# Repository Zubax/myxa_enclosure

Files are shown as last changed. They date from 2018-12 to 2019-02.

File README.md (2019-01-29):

# Aluminum enclosure for Myxa

[**Myxa**](https://zubax.com/products/myxa) is a high-end FOC ESC based on the [Télega motor control technology](https://zubax.com/technologies/telega).

The aluminum enclosure increases the continuous power range up to 850W and provides additional protection against mechanical damage.

You need to have SolidWorks 2017sp1 or higher to open the assembly files. You can also download [eDrawings](http://www.edrawingsviewer.com) for viewing and exporting the enclosure assembly files.

A plastic enclosure for Myxa is [also available](https://www.thingiverse.com/thing:2792733).

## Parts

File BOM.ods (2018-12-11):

Qty | Device | Parts | Description | SIZE | DIGIKEY# | LENGTH | MANF | MANF# | link
3 | HEATSHRINK |  | Heatshrink for phase connectors | D = 4.6mm | X2-4.0-0-SP | 10mm | TE Connectivity Raychem Cable Protection | X2-4.0-0-SP
1 | HEATPAD |  | Heatpad | 35x8x1 mm | P121365-ND |  | Panasonic Electronic Components | EYG-T3535A10A | https://www.chipdip.ru/product0/9000203898
3 | Screw M2.5 15mm DIN912 ISO4762 |  | Mounting screws | M2.5 15mm | 36-29306-ND | ~15mm | Keystone Electronics | 29306 | https://www.mcmaster.com/91290a302
1 | Housing |  | Aluminum housing for Myxa |  |  |  | Zubax | Myxa housing
1 | Printed mount |  | 3d-printed part which serves as standoffs and big capacitor damper |  |  |  | Zubax | Myxa printed part

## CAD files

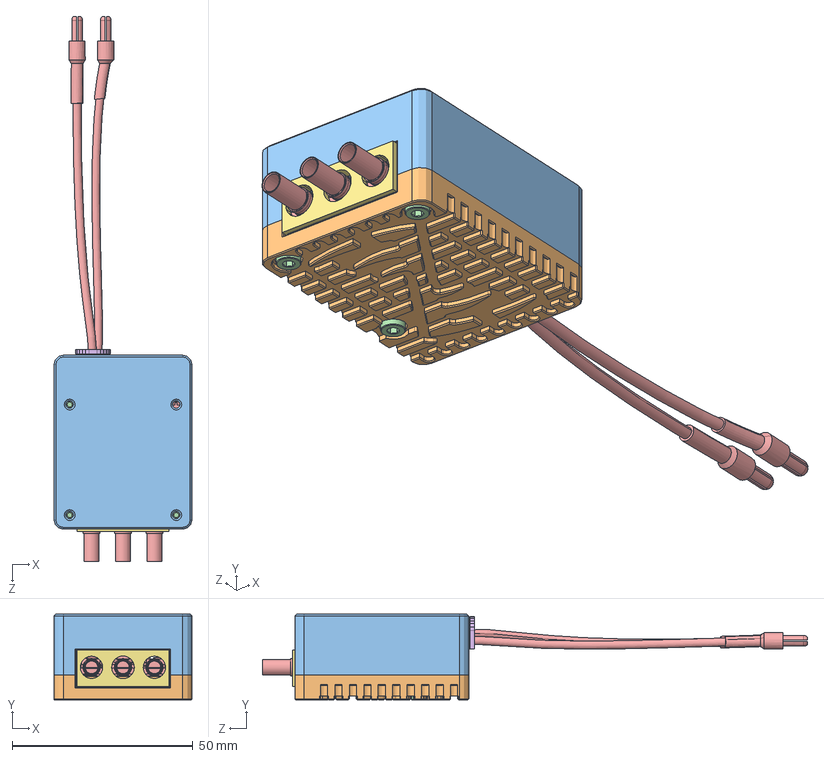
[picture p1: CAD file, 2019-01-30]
myxa_case.sldasm
38.2 x 23.7 x 151.0 mm
washer x 6
case_top
case_bottom
91290A302_BLACK-OXIDE ALLOY STEEL SOCKET HEAD SCREW x 3
myxa
battery_wires_spacer
phase_insert

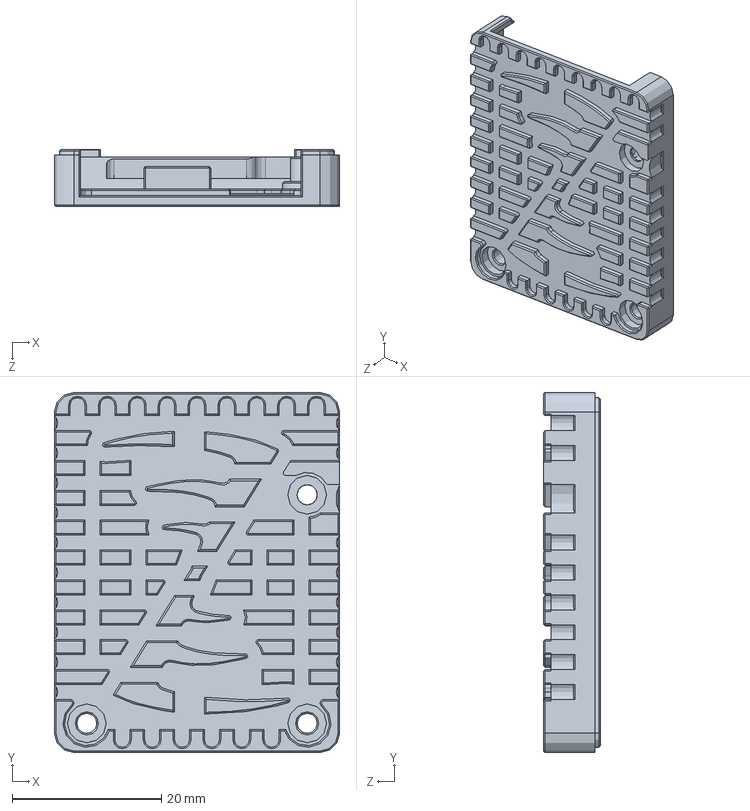
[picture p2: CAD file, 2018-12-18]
case_top.sldprt
38.2 x 48.2 x 7.65 mm

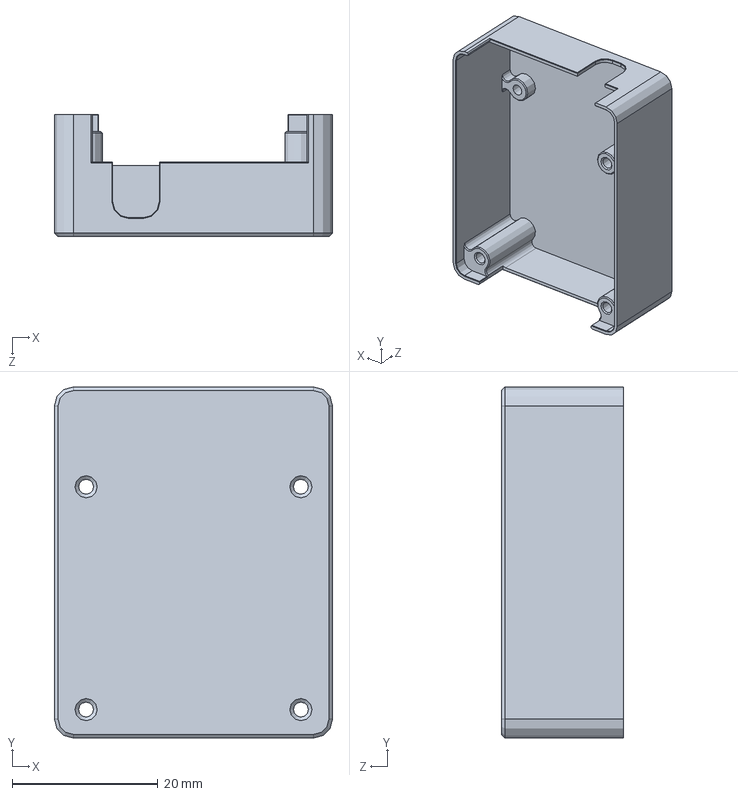
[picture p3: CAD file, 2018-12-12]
case_bottom.sldprt
38.2 x 48.2 x 16.8 mm

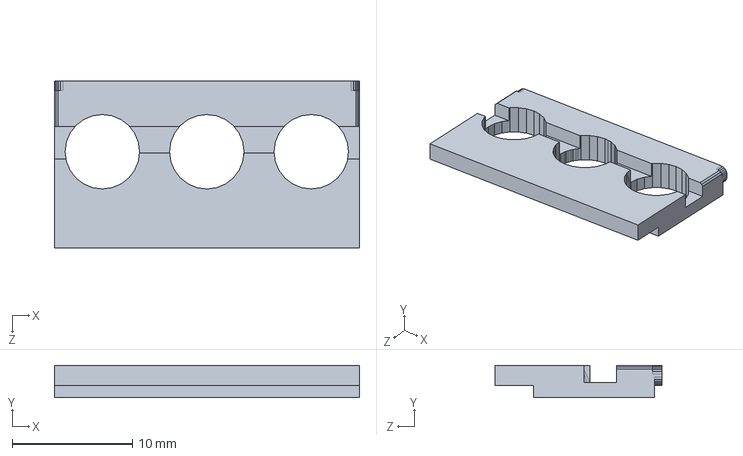
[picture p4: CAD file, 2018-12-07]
phase_insert.sldprt
25.4 x 2.70 x 13.9 mm

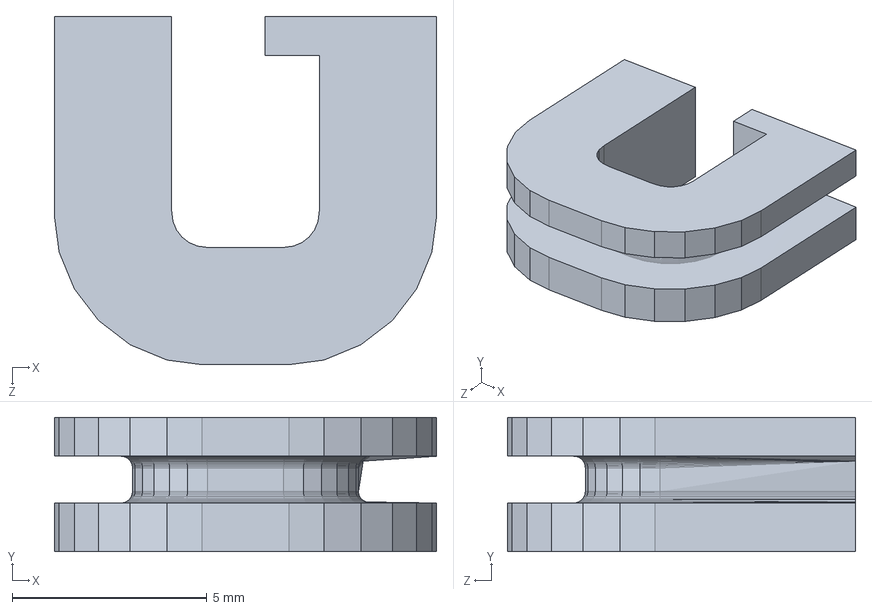
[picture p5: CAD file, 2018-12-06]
battery_wires_spacer.sldprt
9.80 x 3.45 x 8.94 mm

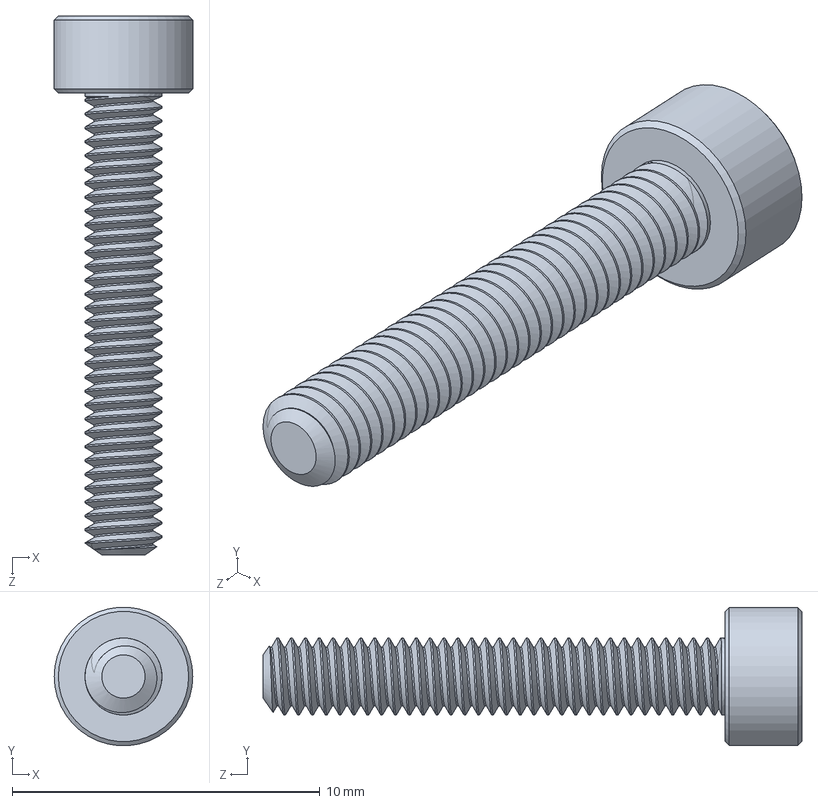
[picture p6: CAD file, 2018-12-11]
91290A302_BLACK-OXIDE ALLOY STEEL SOCKET HEAD SCREW.SLDPRT
4.50 x 4.49 x 17.5 mm

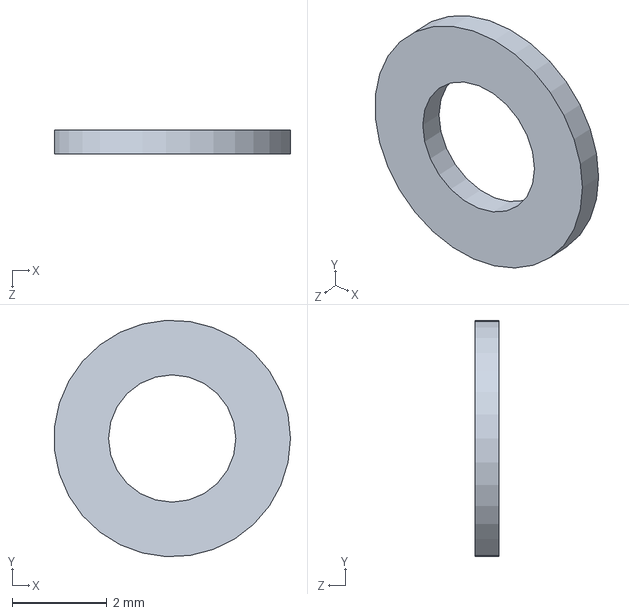
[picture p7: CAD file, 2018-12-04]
washer1.sldprt
4.99 x 4.99 x 0.5 mm

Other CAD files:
myxa_case.SLDDRW

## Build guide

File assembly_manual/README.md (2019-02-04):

# Aluminum enclosure assembly manual

## Parts needed
| Parts | Amount |
|---|---|
| Myxa A/B	 | 1 pcs |
| Aluminum enclosure 	 | 1 set |
| Plastic washers ⌀3 thickness 0.5 mm 	 | 6 pcs |
| 3D printed plastic sleeve set 	 | 1 set |
| Thermal pad 1 mm thick Arctic ACTPD0005A (two layers of 0.5 mm are acceptable but not recommended) | one strip 10x48 mm |
| Steel hex screw DIN 912 M2.5x16mm	 | 3 pcs |
| Zapon lacquer or similar 	| approx. 0.5 ml |

## Tools needed
* Knife
* Tweezers
* Ruler
* Hex key 2 mm (either an L-shaped key or a screwdriver)
* 50 VDC lab power supply

## Assembly
First, prepare a 10 mm wide strip of the thermal pad. Use the ruler and the knife to ensure that the cutoff line is straight. Afterward, cut the stripe into two patches: one 10 x 35 mm and one 6 х 13 mm. 

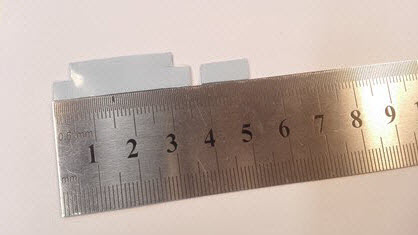
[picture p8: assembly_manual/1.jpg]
Thermal pad strip


Put the three screws into the holes on the top part of the enclosure and insert plastic washers on them.

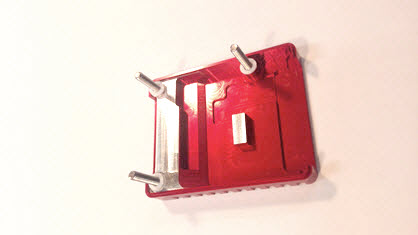
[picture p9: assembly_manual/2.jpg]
washers


Remove the protective film from one side of the patches and carefully place them onto the heat exchange surfaces of the heat sink, as shown on the image. Do not touch the heat exchange surfaces while assembling the enclosure. This is because the grease from human hands may impair thermal conductivity of the interface.
You must ensure that the longer patch is perfectly aligned with the edges of the enclosure. If necessary, use the tweezers to align the large patch at the edges.

When both patches are put in place and aligned properly, remove the protective film from the other side using the tweezers. 

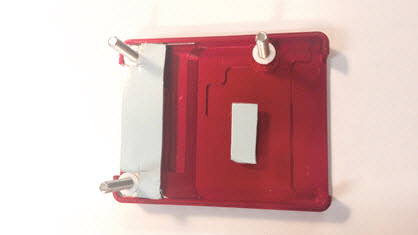
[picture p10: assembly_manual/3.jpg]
thermal sink
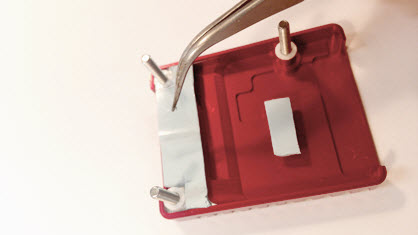
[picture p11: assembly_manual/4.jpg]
protective film removal
   

Slide the 3D-printed plastic parts named `battery_wires_spacer` and `phase_insert` onto the power supply wires and the phase connectors of the Myxa ESC, respectively.

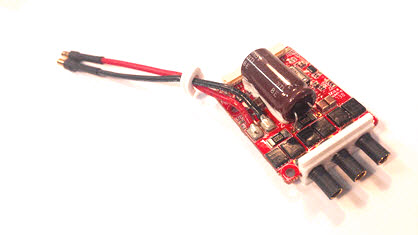
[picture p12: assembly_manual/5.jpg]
sleeves


Mount the Myxa PCB on the top part of the enclosure and insert washers on the top side of the board.  

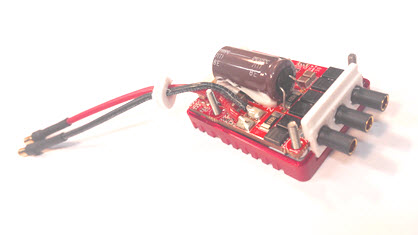
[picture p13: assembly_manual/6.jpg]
myxa mounting
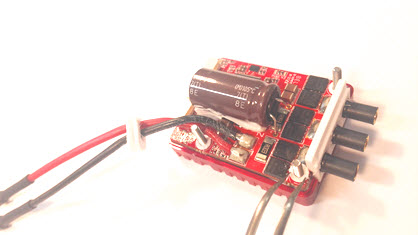
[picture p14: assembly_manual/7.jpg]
washers on myxa
   

Apply varnish/lacquer on the threaded ends of the screws. This is needed to fix the screws in place to prevent unintended disassembly of the device when exposed to vibrations - the varnish/lacquer is acting as a glue here. 
The battery wire spacer and phase insert should be glued in place using the varnish/lacquer too; otherwise, there's a risk that they can move or fall off.

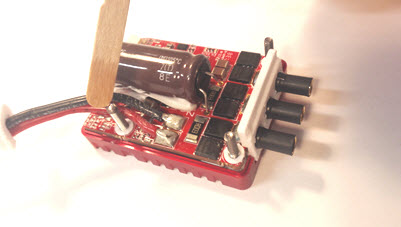
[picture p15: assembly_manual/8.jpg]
lacquer


Carefully lower the bottom part of the enclosure onto the screws. Make sure that the screws are aligned with the holes on the bottom part of the enclosure. Make a few turns of each screw by hand. Afterward, close the two parts of the enclosure.

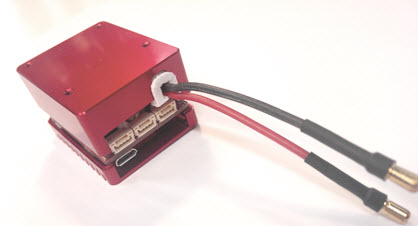
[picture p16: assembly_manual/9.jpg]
bottom mounting
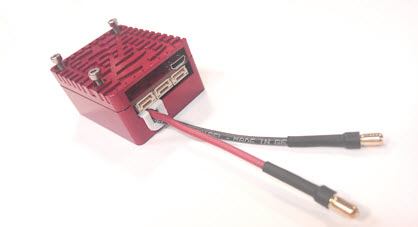
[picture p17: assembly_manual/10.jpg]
final assembly
   

Tighten the screws.

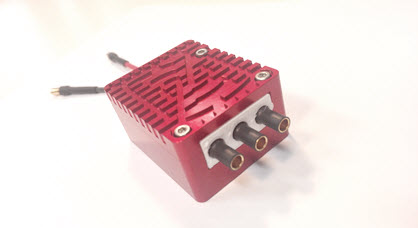
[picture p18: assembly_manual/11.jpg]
tightening


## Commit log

2018-02-01 Cleanup - removed exports and renamed an improperly named directory
    [MUXA ASSEMB Full.SLDASM, MUXA ASSEMB Full.SLDDRW, case_bottom.SLDPRT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]
2018-02-14 Add files via upload
    rubber bushing
    [MUXA ASSEMB Full.SLDASM, case_bottom.STEP, case_bottom.sldprt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]
2018-02-16 visualisation & materials chenges
    [MUXA ASSEMB Full.SLDASM, MUXA ASSEMB Full.SLDDRW, case_bottom.SLDPRT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]
2018-03-08 Cleaned up the file names, fixed typos
    [myxa_assembly_full.SLDASM, myxa_assembly_full.SLDDRW, rubber_sleeve_4x10.5x5.SLDPRT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]
2018-04-25 aluminium housing corrections
    [case_bottom.sldprt, myxa_assembly_full.SLDASM, washer.SLDPRT]
2018-05-01 case_top corrections. 17.4 g
    [case_bottom.sldprt, myxa_assembly_full.SLDASM]
2018-05-25 low profile metall case
    [case_bottom.sldprt, connector_rubber.sldprt, myxa_assembly_full.SLDASM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]
2018-05-25 remove old washer
    [washer.sldprt]
2018-05-25 Fixing after Dmitry
    [myxa_case2_3.sldasm, rubber_sleeve_4x10.5x5.sldprt, screw_m2.5_10.sldprt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]
2018-11-08 More cut for ceramic highvoltage capacitors, Myxa SolidWorks Assembly
    [0402_LED.sldprt, 5-4.sldprt, Board.sldprt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]
2018-12-04 Equal washers and clearences
    [case_top.sldprt, myxa_case2_3.sldasm, washer1.sldprt]
2018-12-04 BOM added
    [BOM.ods]
2018-12-04 Thermal pad clearence is 0.5mm. Notches for plastic washers
    [case_top.sldprt, myxa_case2_3.sldasm]
2018-12-06 meet new Myxa 3dmodel with wiers and plastic inserts
    [0402_LED.sldprt, 5-4.sldprt, Board.sldprt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]
2018-12-07 Some changes of a scene and textures
    [myxa_case2_3.sldasm, phase_insert v2_1.sldprt]
2018-12-11 Screws changed and wachers under the board added
    [91290A302_BLACK-OXIDE ALLOY STEEL SOCKET HEAD SCREW.SLDPRT, BOM.ods, case_top.sldprt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]
2018-12-12 some face and gaps changes
    [case_bottom.sldprt, case_top.sldprt, myxa_case2_3.sldasm]
2018-12-18 mounting bore for plastic inserts corrected
    [case_top.sldprt, myxa_case2_3.sldasm]
2019-01-30 Parts renaiming
    [battery_wires_spacer.sldprt, myxa_case.SLDDRW, myxa_case.sldasm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]
2019-01-31 assembly manual first commit
